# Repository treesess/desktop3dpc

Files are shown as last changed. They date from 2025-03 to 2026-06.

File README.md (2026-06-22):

# desktop3dpc - vcp (vibration cementitious printing)

desktop scale 3d printing of cement-based/non-Newtonian materials (e.g., cement paste, mortar, concrete) using a vibration unit in the toolhead to make the fluid down from the nozzle. 

 **check out the latest version of build:**

- [vcp voron, r11, integrated hopper-nozzle design but no hotend, easy assembly, friendly for starters](https://github.com/treesess/desktop3dpc/tree/main/vCP260622%20vcp%20voron%20r11)
- [vcp voron, r9.3, stable version with hotend, difficult to make and assemble](https://github.com/treesess/desktop3dpc/tree/main/vCP260419%20vcp%20voron%20r9.3)

This page is basically a journal, updating the latest works. 

-------
**260622 update:** 

vcp voron r11 (integrated hopper-nozzle design but no hotend, friendly for starters) has printed 100% size benchy successfully. CAD file has been uploaded. major updates of the design has been documented. 



cosy ship, huh. well, first time for 100% size benchy, so yeah again, room to improve as always. 

i just came to realize that for a print this small, i should turn off the heat bed and pause every single layer and blow it with heated breeze (i.e., hair blower). haha, it worked. 

and keep blowing heated breeze might also work. but it must have programmed pooping and/or wiping to avoid clogging. to be updated later... not likely to add a part fan on the toolhead but more likely to get it a side fan with heat. 

as i said, water control is the center of desktop cementitious print. and heat is one major way to control the water content in the printed part, no matter via hotend, heat bed, or hot side fans. 

the hotend version is not forgotten. since hotend is a better plan than the hot side fans because the side fans cannot blow the heat INTO the printed part but the hotend can extrude uniformly heated slurry and also better for hydration and strength growth. 

-------
**260611 update:** 

vcp voron r10 is on hold while r11 is under heavy tests. 

- r11 is much simpler to make with the hopper, barrel and nozzle printed in one integrated part.
- r11 is easy to assemble with less metal parts but no hotend.
- r11 is very friendly to the starters. that's why i decided to finish up r11 first. 



full video: https://youtu.be/ELNMFBjC2Hw

in the video all was 140% 3dbenchy printing chips. failures were mostly because of mix matter, or feed screw caused pressure builup (so i started to think it's better to switch the feed screw to stirrer only). and simply the difficulties of printing 3dbenchy. 

i have to say benchy is very hard to print. especially when some of the layers have only a few seconds of layer time. 

is this project/toolhead useless since it cannot even print a nice benchy? well, can clay printers do the benchy? lol. thus, i believe the slurry print of this project has achieved much more than expected. you will love vcp voron r11. 

-------------------------------

**260522 update:** spent 4 hr 42 mins printed this giant thin wall vase. not perfect, but learnt sth more and confirmed that the water content in the print body determines it's being "wet print" or "dry print". Also, the chamber humidity greatly influences the water content in the print body (yea you already guessed that). related Reddit post: https://www.reddit.com/r/3Dprinting/comments/1tkmnuv/desktop_cementitious_print_by_vibration_vcp_voron

starting do the enclosure for this printer with a humidity control plan (no way, i do know humidity control isn't easy. hope the accuracy of humidity control for vcp isn't that harsh).



(left: eSUN PLA+ fire engine red; right: cement paste; both: printed by VORON2.4)

Model credit: A *slightly* Overengineered Olpe Vase by Nat on printables: https://www.printables.com/model/290951-a-slightly-overengineered-olpe-vase-print-in-vase

-------

**260517 update:** vcp voron r10.1 is being tested. so far so good. use 20.5 mm barrel and a feed screw having a large gap with the barrel. 

this means:

a) less assembly precision needed 

b) pressure buildup inside the barrel will be mostly turned into backflow, which means better mixed slurry, and

c) the problem of jam due to pressure buildup will not happen again. 



-------

**260513 update:** layer lines. what layer lines?



mortar this is. added 40-70 sand. 

model: Queer_Qube_Box_50mm.stl by DaveMakesStuff on [thingiverse](https://www.thingiverse.com/thing:6321660).

-------

**260508 update:** have been testing 1.5 mm nozzle using my ocd for days. it's bloody hard and i came along with concepts that i didn't know before. some kind of pressure build-up when using feed screw which caused blockage/choke-up. planning to redo the screw barrel to 20 mm diameter and have more tolerance for the backflow. 



Juliavase and 30 mm VORON DESIGN cube have been printing for days. i will get a perfect one.  

and yes, new feature unlocked: pigment efflorescence (in a good looking way)

-------

**260423 update:** finally got the perfect VORON cube (i mean, the mechanism reached the "perfect" level i expected for months). will still keep exploring. 

check out the video clip on [utube](https://youtu.be/D2BQ4VoVuh0)



-------

**260329 update:** after printing ten plus VORON cubes, i tried a benchy. not that the VORON cubes are not good to show, but i want a perfect VORON cube next time i post it. 



-------

**260208 update:** in case you are interested in how it looks after curing, the photos fyi. smooth skin of it, makes us can't stop rubbing it. 





also the non-vase mode (normal slicing, not using spiral/vase mode) print has been tried. several times: 



hey, it's a VORON cube i believe, i know it's not cool enough... could you pls just give me some credits for trying the predicted disaster XD. 

yes, the flowrate wasn't good, due to, umm, some print parts cracked not long after the start of printing. 

also of also, the MCU error (actually tmc2209 drive error) has been fixed by updating the toolhead - sorry that version is not milestone enough so i may upload an even newer version after finishing the design and test. 

i think i also need to explain why there was stepper drive error. it's some kinda "reverse electromotive force", caused by the obvious - we force the stepper to lose steps all the way, so when the rotor kept bouncing backwards again the drive, thus the "reverse electromotive force". sorry that i can only explain this in a level of "making sense" because i m not a specialist on motors... 

-------

**260108 update:** though the MCU (skr pico) reported error from time to time (possibly due to the intentional step loss of motor), a neat enough one has been printed: 



above is the latest print. 

------

**251007 update:** shore 10 solid silicon rubber (SSR) applied as a buffer to isolate the vibration from the toolhead to the printer frame. Metal nozzle adopted. Vibration motors directly hits on metal nozzle. 4 mm nozzle printed cement paste with a stable flowrate. 



(this was printed by a subversion toolhead, which was not uploaded, but don't worry the current version is much better.)

--------

below is my first print:



1) put a vibration device just above the nozzle. not a stirrer but an actual vibrator. 
2) heat bed on, like fdm

in this way, you can easily print cement-based stuff to whatever height you want on a desktop. 

no need of any additions (e.g., PFA, GGBS, silica fume, plasticizer, AC, balabala), just OPC and sand can work this through. 



i used modified CR10s as the motion system, changed the toolhead, and printed about 300 mm wall in vase mode with about 20 mm thick of width. 

you may see the flow rate unstable in the picture, that's because i just came up with the vibrator idea last night and was controlling the flow manually. surely will do a better control of flowrate. 

-----

the advantage is clear: 

1) no need of pump, which is a must in industrial printers.
2) no need of additions, which make it pretty easy for raw material prep.
3) water/cement ratio can be seriously low. 
4) Klipper firmware and fdm slicer can do most of the gcodes, easy for turn a digital obj into print file.
5) simple toolhead, basically every fdm machine can be modified into a cementitious material printer with a slight change of toolhead.

----

note: 

1) for sand, you better sieve it into 0.3 to 0.6 mm size. of course, if you use a larger nozzle, you can even do coarse aggregate (5 mm or above).
2) heatbed greatly reduces the first setting time of the fresh mix. but it might affect the final strength of the print. however, it's desktop, you want the shape but not the strength, don't you?

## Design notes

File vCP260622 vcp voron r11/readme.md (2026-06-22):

r11 is a plastic nozzle version without hotend to heat up the nozzle but very friendly for starter to build. low cost and easy manufacture/assembly.

documentation in coming!

if anything doesn't seem right, my apologies. please let me know. Thanks!

-----------------------------------------

# 1 toolhead, vcp voron, r11

just a second for the naming of vcp voron: vcp is short for vibration cementitious print, vcp voron is like E3D Revo Voron, means vcp *for* VORON since it's based on VORON2.4 motion system. previously there were vcp on a CR10 but that's not reliable since the bed of i3 motion system is not good for the fresh slurry print to keep its shape. so basically vcp is just for VORON (or delta, but still DORON Velta would be nice). 

## 1.1 toolhead intro

i hope this intro shows you how this toolhead works. parts were put into folders.

### 1.1.1 x carriage

based on the x extrusion and MGN12 linear rail of VORON2.4r2.



### 1.1.2 positioner

to make the major functional part in position, as well as connect to PG13.5 umbilical cable mount. 



### 1.1.3 integrated hopper-nozzle

cementitious slurry goes in from the top and comes out from the bottom. 



### 1.1.4 hypocenter

this group generates pulse vibration by forcing step loss of the stepper. no worry about the counter-EMF (counter-electromotive force), the 608 bearing limits it and i tested it.



the hypocenter has been working very stably through many versions in the prototyping. the hitter is an M3x50 screw with many shims to thicken it a bit.

### 1.1.5 (optional) upper drive

actually became optional. the major function of this part is to keep stirring the slurry so that it won't settle in the flow path. you can do the stir-up manually without this part. 



for nozzle diameter smaller than 1.5 mm, it's NOT recommended to install this part (and yes stir up the slurry manually would be an better option, i will explain why later (maybe...)).

### 1.1.6 (optional) LED light bar

have a better view. 



### 1.1.7 (optional) resin coating jig stand

if you want to finish up the surface with epoxy resin, you may use this jig. 



# 2 hopper-nozzle body

slurry feed hopper with integrated nozzle printed in one part, brings you a continuous and seamless flow path with smoothness. 

### 2.1 FDM print of hopper-nozzle body

recommend ASA or at least ABS print of the **hopper-nozzle body** because cementitious material is alkaline (pH 12-13 for fresh slurry) therefore PETG or PLA won't survive too long. 

0.2 mm layer height is good. recommend 0.5 mm line width for both inner and outer walls with 7 walls at least, because it's gonna stand against frequent impact pulse vibration during the print. 

after print out, directly screw in one M3x20 SHCS (socket head cap screw) near the nozzle as a reinforcing bar, like this: 



(do not over-fasten this screw, it's plastic anyway. over-fastening may cause interlayer cracks in the print part)

### 2.2 (IMPORTANT) internal flow path finishing procedure

the flow path needs to be smoothed by drill bits, 60° chamfer drill bit, files. the roughness of the flow path will cause flow rate inconsistency and/or material buildup and/or clog. 

tools need: 



- hand-held electric drill (better have 2 sets)
- 20.5 mm 60° 3-flute chamfer drill bit  (*filleted, extended*) - M3 or M4 tapping tools are needed to extend the length of this bit (see photos below)
- (optional) 20.5 mm drill bit
- hex shank screwdriver bit extension
- hex shank socket wrench 
- round file
- nozzle-diametered drill bit (e.g., 1.0 mm drill bit if you want 1.0 mm nozzle diameter)
- (optional) carbide rotary file (pointer)
- 4-flute taper reamer with hex shank socket (*tip sharpened*)

(optional but highly recommended) you may use an angle grinder and sandpaper to do a fillet on the sharp edge of the 60° chamfer bit. this can give you a smooth transition of flow path. 



a light torch is recommended if you wanna have a look of the flow path:



#### 2.2.1 section one - barrel

you can consider using a 20.5 mm diameter drill bit, but personally i only use the 20.5 mm 60° chamfer drill bit. 

(optional) 20.5 mm drill bit: 



(must) 20.5 mm 60° chamfer drill bit:



i recommend doing this section dry.

if you ever have the other way to drill it down to the throat of the flow path, you don't need to do the extension of the 60° chemfer bit. if not, my plan is tapping the hold of chamfer bit and use an M3 or M4 SHCS and hex shank extension to reach the throat. 

hold the print part and drill in the chamfer **slowly**. 

**PLEASE BE SLOW**. or you may hurt yourself or waste the print part.  



don't do it to the throat in one go. drill in 10 or 20 mm and retreat once. repeat  till you see something like below, you've reached the throat: 



#### 2.2.2 section two - throat

these three are for the throat:

- 4-flute taper reamer
- round file
- (optional) carbide rotary file



if you have the carbide rotary file, you may not need to sharpen the tip of taper reamer like i did. if you don't have the rotary file, you may need to shape the blades on the tip of the reamer. 

let me know if you have better tools for this job! 

for this part, sorry that there is no good photo to take since it's deep inside. 

for me, i use the round file as a probe to grope 



there should be NO STAIR(S) on any transitional part of the flow path. any stairs are meant to make some material buildup during slurry printing. 

#### 2.2.3 section three - nozzle

slowly, drill in your preferred diameter drill bit from the other end like this: 



again, it's better to advance 2 mm and retreat once. repeat till you get it through (to the throat). 

#### 2.2.4 repeat section two and section three multiple times

please repeat section two and section three multiple times and end it up with section two as a finishup. i don't know how to explain this. hope i m scientific enough. 

test it with water. water goes in from the hopper end should be able to come out from the nozzle by gravity:



### 2.3 outer perimeter of nozzle

this is how it looks like when finished with the above steps:



we need to cut it sharper. theoretically, anything sharp enough can do this. you can even use a soldering tip to do this (but i don't recommend that). 

my choice is ultrasonic cutter (e.g., Magicutter): 



the ultrasonic cutter is easy to use and can slightly melt the ASA print making it smoother. 

make the nozzle perimeter as thin as possible (the thinner the better print quality but harder to make): 



(optional) you may file the perimeter a bit if you like: 



then sanding it with at least 2500 grit sandpaper **with water**: 



this would be okay (the perimeter should look polished): 



### 2.4 buffer for positioner

i use PTFE tape as buffer. you can also print a TPU one (like the one in r9.3).



(optional) and wrapped up by some kind of tape that water cannot wash away: 



(optional) better write down the nozzle diameter on the body:



### 2.5 bearing retainer

M3x4x5 VORON standard heat inserts set in the FDM printed bearing retainer part. also here are one 608 bearing and two M3x40 SHCS.



preload the 608 bearing into the retainer: 



screw up the two of M3x40 SHCS: 



### hypocenter

*to be continued*

*to be continued*

*to be continued*

now it's ready to be installed on vcp voron toolhead.

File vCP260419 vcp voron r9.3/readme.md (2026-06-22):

r9.3 is a version you can build and do stable prints. 

documentation for details coming soon. 

if anything doesn't seem right, my apologies. please let me know. Thanks!

# 1 basis of slurry/cementitious printing (IMO)

## 1.1 FDM and slurry printing

hope these texts help you understand the essence of printing. 

with the same kind of motion system, FDM and cementitious printing are quite alike. the differences are:

FDM is centered on **heat**:
- heatsink
- hotend
- heater bed
- melting point (despite plastic types, heat determines the flowability of plastic) 
- chamber temperature
- part cooling (heat dissipation)
- balabala you name it

cementitious printing is centered on **water**:
- water/cement ratio (or water/binder ratio)
- water evaporation
- hydration (chemical reaction between water and cement to get hardened)
- viscosity (despite ingredients, water determines the viscosity of slurry)
- heat (heat accelerates water evaporation)
- breeze (accelerates water evaporation)
- potato flour in breeze (absorb the water on the extruded slurry)

though heat and water are two different things, however, the logic is the same: *we want it to be liquified to extrude, and solidified to fix the shape.* FDM does it via heat, cementitious printing cuts it via water. 

by applying heat to cementitious printing, there might be concerns about strength compromises. yes, if you heat up the slurry too much, bad things happen (cracks, hollow inside with thin crust, lower final strength etc.) imo these can be handled by adding UEA, SF, etc.

surely you don't want to cook the slurry. the strength matters are actually demand matters. what is the print for? answer this then consider heatup or not. heat is to make the print much faster, but not a must (especially when you don't like it (but i do like it xd)).

## 1.2 mix design

mix design refers to the composite of your mix. i will try list the items i know (correct me if wrong, i m just an amateur). 

| item | purpose |
| --- |  --- |
|water| to hold everything together, the pure the better|
|OPC (Ordinary Portland Cement) 52.5 N  |major binder, react with water to build up strength (hydration reaction) |
|PFA (fly ash) |  secondary binder, helps with crack, makes the slurry less bleeding etc. |
|GGBS |  secondary binder, get strength somehow faster comparing to adding PFA |
|sand |fine aggregate, imo make it easier to print|
|stone |coarse aggregate, often larger than 5 mm diameter， thus not likely to use on desktop level, unless you are printing something rough with nozzle diameter larger than 10 mm |
|SP (superplastisizer) or plastisizer (liquid) | make the slurry better flow with less water |
|retarder | similar to SP, but slows down the chemical reaction to buy your longer printing time|
|SF (silica fume) | fine particles help to get compact print|
|quartz power 325/600 mesh | filler, makes the print compact|
|UEA U-type expansive agent | avoiding crack, very useful|
|iron black, iron red, iron something |pigment. may need more water if you add pigment |
|...|...|

## 1.3 how to start first mix desgin

if you are not familiar with cementitious, start with an easy one using only OPC, water, and fine sand (40-70) is totally okay even for 1.5 mm diameter nozzle. recommend w/c = 0.4~0.5, cement to sand 1:0.5 for starter. if you find it hard to mix up (too viscose), try adding a bit more water is fine. weight up mass but not volume. 

if no retarder or PFA added, you have about 1 hour to print. the longer you wait, the harder the mixture is. if you try to add more water after 1 hour to make it printable, the final strength is likely to be compromised somehow, but you can do this for the first several prints since you will need some time to feel and understand it. try and error with more or less water is a good exercise to grasp it. 

if you can handle printing the simple formula, then go considering adding UEA, SF, and retarder to get better/consistent print quality. 

if you are an expert, don't take anything i say seriously and correct me if anything is wrong. Appreciate it. 

## 1.4 how to mix

**safety/health first, get N95 dust mask to protect your lungs.** protective glasses, nitrile gloves (cement-based materials are alkaline (pH value can get to 13)). well, this is the highest standard of protection maybe. personally, i would also recommend gentle, gentle, gentle handling of all the powders to avoid dust flying up. 

dry mix first, wet mix next. 

- dry mix means get all the solid particles measured by mass correctly in a container, then gently, gently, gently mix them up. the colors of different ingredients are likely to be different, so if the final color is uniform, your mix should be fine. do more mixing if unsure. take your time.
- wet mix means adding water to the well-mixed dry mixture from the previous step. prepare your clean/pure water with SP or retarder before adding to the mixture. you may use a syringe/pipet to add the exact mass of water (and other liquid additives) as designed. still, gently, gently, gently add water into the mixture. take your time. start the wet mix slowly. after you see no dry particles, you may mix it faster.

if you add SP or retarder, you may also need to mix for a longer time. by adding retarder, you may use less water and have very long printable window (like 2~3 hours, i tried 5 hours tops, but that was bad). for large prints, i would prepare the dry mix in separate covered containers in the first place, then only add water for wet mix when needed during printing. try not to wet mix over 400 grams anytime. for me i wet mix 100 to 200 grams per batch. 

these are the basics to start with. i think you can start your first mix safely with these recommendations.

for more details, please find tutorials or your expert friends. welcome to email me any questions. 

one further tip here: if you use sand, note that sand absorbs water and releases the air inside it. therefore, you need to vibrate it before your actual printing. i just put the mixture into the toolhead hopper and start extruding/vibrating, then catch the slurry from the nozzle back to get rid of the air bubbles. so is the coarse aggregate. 

---------------------

# 2 vcp toolhead

## 2.1 toolhead intro

i hope this intro can show you how this toolhead works clearly. parts were put into folders. 

### 2.1.1 x carriage



based on the x extrusion of VORON2.4r2. 

### 2.1.2 positioner



to make the major functional part in position, as well as connect to PG13.5 umbilical cable mount. a thick TPU ring is between the major part and the positioner as a buffer. 

### 2.1.3 feed screw and barrel



paste put in here. this group includes the feed screw, screw barrel, stepper, Orbiter planetary gearbox, stirrer, etc. the feed screw provides better extrusion accuracy. the stirrer avoids material buildup inside the hopper. the stepper and the gearbox drive them. 

### 2.1.4 hypocenter



this group generates pulse vibration by forcing step loss of the stepper. no worry about the counter-EMF (counter-electromotive force), the 608 bearing limits it and i tested it. 

### 2.1.4.1 stepper with hitter 



sorry i don't know how to name it. this group inside the hypocenter has been working very stably through many versions in the prototyping. the hitter is a M3 screw with many shims to thicken it (try any other metal way to make it as you want). 

### 2.1.4.2 608 clamp and hotend



the hitter driven by the stepper hits the 608 bearing, where the heat block is locked tightly by 3x M3 screws so that the vibration can be passed to the nozzle in a rigid structure. the heat block is the CR10 one. the nozzle is SUS304 tube been cut and tapped with M6 threads. 

-------

## 2.2 make of toolhead parts

### 2.2.1 FDM printed parts

- since almost all parts are under cyclic load, ASA is recommended for the printing of vcp voron toolhead with 0.3 mm layer height. 
- for the barrel/hopper one, 0.1 mm layer height is recommended to make a smooth inner surface of the barrel as possible.
- for the feed screw, 0.1 mm layer height is recommended. better sand it smoother. 
- get some more perimeters and higher infill percentage as possible. sorry i don't have tests to tell how strong they need to be. 
- there is only one TPU part. you need to cut it vertically after print. if you don't want TPU, you can just use some tapes (PTFE Tape i recommend).

### 2.2.2 metal parts

- the M3x100 SHCS needs to be straight.
- the M3x100 SHCS needs to be straight. 
- the M3x100 SHCS needs to be straight. 

this M3x100 is to strengthen the feed screw. i may try metal print of the feed screw later. 

### 2.2.3 heat set inserts

only the "standard VORON heat set inserts" M3x5x4 mm is used. 

- 4.6 mm holes are for heat inserts
- 5.7 mm holes are for SHCS caps

*to be con't*

-------

## 2.3 toolhead assembly

there is no screw must be fastened very tight to make it work. overtighten might cause plastic failure or fail of assembly (i've been there). 

### 2.3.1 x carr 



- 2x M3x40 SHCS to assemble the left and right parts.
- 4x M3x8 SHCS to fix the x carr parts to MGN12H slide block with belts through. similar to the original x carr. 

btw i kept the 32.5 mm horizontal distance of screw distance for the x carr but the failed to follow the vertical distances. 

if you need to change the x carr frequently, i would recommend marking the belt as in the photo. 

### 2.3.2 hypocenter stepper w hitter



### 2.3.3 pancake NEMA 17 w Orbiter planetary gearbox (8 mm shaft)



### 2.3.4 hotend (2x CR10 heat blocks)



drill out the M6 threads of the upper one or not seems does not matter. 

### 2.3.5 feed screw w stirrer



get a 0.5 mm M3 shim in between the feed screw and stirrer is recommended. 

### 2.3.6 coupler



screw the M3x100 tight now. but not too tight to break the plastic...

### 2.3.7 to the pancake



### 2.3.8 into the screw barrel



### 2.3.9 tight up pancake mount



check if you can rotate the feed screw and stirrer manually. if you can't, try loose the four mount screws a bit. 

the feed screw should not have relative rotation to the stirrer. or you need to check step 7. 

### 2.3.10 hypocenter motor



watch out the cable exit and hitter direction. 

if you feel it time consuming to screw in these two M3, just drill the motor mount with a 3 mm drill bit. 

don't overtighten these two M3. 

### 2.3.11 checkpoint



### 2.3.12 nozzle



it is SUS304 tube, OD 6 mm ID 3 mm. thread the tube with M6 so that you can get it into the CR10 heat blocks. the total length doesn't have to be accurate. not even the length of threads. just about 40 mm long is fine. you will find out why when you finish the assembly and G28 z. 

### 2.3.13 nozzle assembly



screw the nozzle into the CR10 heat blocks and push it into the lower end of barrel. there should be a small gap as shown in the photo. don't really matter how large the gap is. or you can use a feeler gauge to be certain. just define the gap by yourself. sorry i m lazy to do that. 

### 2.3.14 secure the nozzle



- two M3 screws first
- M6 nut later

### 2.3.15 608 clamp







set steppers off, and move the hitter manually. it should be free to move several millimeters with the limit of 608 bearing. if it's too tight to move it. try loose the two motor screws a bit or the clamps and twist it a little. 

### 2.3.16 TPU buffer



### 2.3.17 fake position



since i don't have xyz endstops for now. i fake the position at 150 0 0 and manually set z offset. there is no QGL so far. sorry. 

### 2.3.18 tighten up the positioner parts



and the PG13.5 umbilical cable mount. 

the optional COB LED light bar is also included in the cad file .f3d. just hook it up if you make it too.

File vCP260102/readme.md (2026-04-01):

this is a vCP-e version where e for extruder axis in use. That is, FDM CAM slicers (e.g., OrcaSlicer) with default E gcode generation can be directly used for this toolhead in a print. 



yes it's already this good without detailed tuning. check out how it moves: https://youtu.be/I5zWxPGP2qw 

the greatest benefit of using E axis in FDM slicer is that, you can do perfect *TRAVEL*, i.e., you can move your toolhead without leaking a single bit of cementitious mixture! 

recommended Klipper configuration for extruder:

```
rotation_distance: 5  ; this affects the pulse your drive sends to the motor if i m not wrong. to be simple, the smaller this is, the higher frequency the stepper does. 
microsteps: 8   ; or 16 is fine if your MCU doesn't report errors. 
full_steps_per_rotation: 200    ; for 4240 1.8 degree stepper motor
; gear_ratio is not needed

```

and its drive: 

```
interpolate: False  ; i don't know, LLM told me so
run_current: 0.5   ; worked longest for me. smaller run current can make your stepper not that easy to fail under fatigue caused by cyclic impact loading. 
hold_current: 0.5  ; better keep it same as the run_current

```

All CAD and 3MF uploaded for your reference. this version is much stabler than any of the previous versions (including many versions never uploaded...)

BOM of this toolhead: 

| name | qty. | descriptions  |
| --- | --- | --- |
| stainless nozzle |1 piece |dimensions pls see the f3d CAD file thx|
| steel rod | 1 piece |diameter of 6 mm, length of at least 40 mm (hold it, you may need longer for the next version...) |
| M3x80 SHCS | 2 pcs  | for the upper part of mounting|
| M3x50 SHCS | 2 pcs  | for the lower part of mounting |
| M3x8 SHCS | 7 pcs | |
| Heat set inserts (M3 Threaded Insert ) | 3 pcs | The VORON "standard" ones (M3x5mmx4mm)|
| LSR (liquid silicone rubber) | 7 pcs |  20  degree or lower. 50 grams (A+B) is enough for one cast of the rubber buffer parts|
| stepper motor |1 piece |  4240 or longer | 



printing recommendations:

- PETG is recommended for all the parts. 

- Only the bowl part needs a bit support (sorry for that, i don't want to but that's quicker. and i m not sure if the ears of the bowl can be cut off. better have them to simplify the installation). All other parts can be printed without support. You can use PLA to print the molds for LSR if stringing is a big issue for you. 

- maximize the wall/perimeter counts for all parts (except the "front" part) since they are going to suffer from heavy fatigue loading. i ve made them skinny as i think good enough so even if you print all parts in 100% plastic inside, it's not much heavy.



for the "bowl" part, only a bit of support have been painted in the .3mf fyr. 

for casting LSR, please screw your long M3 SHCS into the molds first, similar to the below photo (sorry that the below photo is showing a previous version but i m sure you can get what i mean): 



more info about using SSR for vibration buffer can be found [here](https://github.com/treesess/STEAMRELAY/tree/main/showcase/251003%20vibration%20absorbing%20design%20using%20SSR)

------------

still testing stuff. but the news is, this version of toolhead is still not my ideal plan. new toolhead is on the way.

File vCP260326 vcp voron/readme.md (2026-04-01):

finally i've got a stable version of toolhead. still, too many to improve, trying very hard every day. 

pls see the f3d CAD file for details. 

if you wanna build one, please let me know and i will sort things up and upload them for you. 



The motion system is VORON2.4. X carriage is in the f3d as well. For the modification of bed into a seperate/independent one (to isolate vibration from the frame to the bed), i used a piece of concrete and 4 rubber footpads, not a neat design, may upload later. 

## 1 Explanation of how this toolhead works

1) generation of pulse vibration

Using an M3 bolt as the oscillating impactor, repeatedly tapping the inner race of a 608ZZ bearing to induce periodic (pulsed) vibrations. This M3 impactor was driven by the 42 stepper. The 42 stepper simply executed the gcode of normal E instructions but lost most of the steps due to the constraint of 608 bearing. 

the 608 bearing was tightly constrained with the heat block. the SUS304 tube was tapped and screwed through the heat block. in this way the pulse vibration was passed to the tube. 

2) flow path

the mixture was added into the hopper. since the vibration of the toolhead, the mixture went down by gravity then entered the SUS304 tube. the lower end the the tube was the actual nozzle as the exit of mixture flowing on to the print layer. 

3) why vibration works

cementitious materials are thixotropic, simply speaking they stay sold when static, but become fluid under vibration. we control the vibration of this toolhead, when the toolhead moves to the position to extrude, vibration starts so the mixture become fluid therefore goes down under the gravity. after the extrusion, the mixture stays on a static bed, therefore becomes quite solidified to support other layers. we can do travel without extrusion with the same logic. as long as we don't vibrate, there is no extrusion. 

4) heatbed and hotend

heatbed with 50 to 70 ℃ can accelerate the hydration of cementitious materials. hydration is the chemical reaction that makes the cement-based mix sold permenantly. but temperature too high may cause shrinkage of the print. in real case this doesn't hurt too much because the new layers bring water to the previous layer, to keep it wet. however, overall speaking the chemical reaction needs water to go on, therefore at some point we add water to the print to keep it wet. this is subtle, can only spray a bit because too much water will destroy the print since it needs hours to complete initial setting. the print is vulnerable before that. that's why we need a separate/independent bed for it. 

hotend is experimental. as we heat up the mixture in the toolhead, it increases the workability of mixture and makes it easier to extrude. higher temperature also makes the extruded part cure faster. but there are problems with this doing. if the mixture has been staying in your hopper for too long (1 or 2 hours), it's partially cured, higher temperature make this quicker. the worst case is, when you pause the print, the mixture near the nozzle may complete the initial setting and block your nozzle. 

both heatbed and hotend have another problem, that, higher temperature dry up the mixture and print fast. we really want to keep the water in our mixture because that makes the viscosity stable thus stable flowrate. but heat evaporates the water so this is a subtle balance game. 

5) printing

it is very similar to FDM printing. but much slower. 10 mm/s speed is considered high to me. if one layer has its layer time under 1 minute, it's very likely the next layer will drag it forth and back. so i recommend making a PAUSE to these fast layers. i don't recommend you to slow down these layers since you will need to tune the flowrate for different speed. 

large overhang and medium bridge are all possible. because the mixture is sticky. you may easily print a large overhang successfully, but please wait some time before printing the next layer because it needs more time to set. if you don't wait, the next layer might crush your beautiful overhang. same thing to bridging. 

for large area of bridging (such as the ceiling of 3dbenchy, 250% size), it's totally possible, but, you need to PAUSE every 2 to 3 lines. or the next line may drag the previous line down. 

(to be continued)

## 2 cement paste mix design

i used a simple mix for multiple print tests so far. 

| item | gram | descriptions |
| --- | --- |  --- |
|OPC (Ordinary Portland Cement)|100|major blinder|
|PFA (fly ash)|40|secondary blinder|
|water|50| may add more if your mix is too viscous|

adding river sand (fine aggregate) can improve print quality greatly sometimes, but make sure your sand particles are much smaller than your nozzle diameter (at least 1/2 or 1/3). reduce your water/cement ratio to avoid bleeding and segregation. 

(bleeding means water comes up when vibrating, segregation means aggregates sink down when vibrating.)

(to be continued)

------------------

**important note: everything is still experimental, though this version is basically stable but still need long term tests to prove the robustness which in still ongoing**

## 3 BOM

| item | qty. | descriptions |
| --- | --- |  --- |
| 608zz bearing  | 1 |as the constraint of M3 impactor |
| SHCS M3x100 | 2 | fastening the heat block to the hopper |
| SHCS M3x70 | 1  | ditto |
|SHCS M3x35 |4 |fastening the front and the toolhead to x carriage |
|ASA or ABS filament | - | for printing toolhead components, PETG is not okay with highly alkaline cementitious mixture|
|TPU filament |-| for printing the buffer cylinder which holds the major part|
|SUS304 tube od6 in3, 112 mm long|1| lower end as the nozzle, upper end connects to hopper, you may need longer or shorter depending on bed setting|
|42 stepper |1 | to drive the impactor (hitter in CAD) |
|...|...|...|

(to be continued)

## 4 tools
| item | qty. | descriptions |
| --- | --- |  --- |
|angle grinder|1|you may need to cut or grind the hardware|
|taper reamer bit|1|for chamfering the hopper to make it smooth|
|chamfering bit 60 degree |1| for chamfering the SUS304 tube |
|round file 600 grit|1| to make the tube smoother even|
|1000 to 5000 grit sand paper|1|to make the tube extra smooth|
|angle grinder|1|you may need to cut or grind the hardware|
|allen key|1 set| for the M3 bolts|
|hex bit and screw driver|1| some M3 bolts are too long to be driven by hand|
|containers and mixing knife|3|for mixing cementitious materials, get some spares|
|digital balance, 0.1 g resolution|1-2|for weighing up raw materials for mixture|
|bucket with water|1|for cleaning. when a container or tool with mixture is done, put it in water, this makes it easy to clean later|
|tapping tool M6|1|to tap the SUS304 tube|
|drill bits 6 mm|1 set|make the holes on heat block a bit larger|
|...|...|...|

(to be continued)

## 5 assembly

this toolhead needs certain sequence to assemble. 

1) the "compressir" part to hopper with M3x70 bolt. use both M3x100 bolts for alignment. after aligned, tighten the M3x70 then take out M3x100.

2) screw the tube to the heat block. then get the tube through "compressir 2" and the "compressir" and reach the end of hopper.

3) adjust the screw of tube to make it look fit (um... i don't know how to describe here). the tube is expected to be limited by the hopper and there should be no gap between all these parts.

4) two of M3x100 go through both heat blocks and compressirs to the hopper and screw in the heat set inserts.

5) get the TPU cylinder, knife it so that you can wrap it around the "compressir"

6) get the "front" and its retainer (is it right to call this thing retainer?), wrap the assembled part and use 4 of M3x35 screws to position it to the x carriage. don't tighten, we will need to rotate it and making some adjustment later.

7) assuming you have install the impactor on the motor shaft **(more details need to be explained here)**, install the motor mount to the motor. then use two of M3x?? to fix the motor on the "compressir".

8) put 608 bearing to it's clamp and install the clamp to the lower heat block. make sure the impactor go through the 608 bearing. **(more details need to be explained here)**

9) make adjustment to make sure:

   a) the motor body doesn't touch anything;
   b) the impactor can click the 608 bearing manually **(more details need to be explained here)**;
   c) the installation height is good and the nozzle isn't hitting the bed.

11) fasten the front M3 to finish. these M3 can be used to adjust the nozzle to be parallel to the bed. 

(to be continued)

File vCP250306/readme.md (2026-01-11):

this is an OLD VERSION of toolhead, please go to https://github.com/treesess/desktop3dpc/tree/main/vCP260102 to see the current version. 

-------------------

this is the first design of vCP. based on the motion system of CR10s, changed the x carriage and toolhead and succeeded in stable flow rate mortar printing. 

**all CAD STL are open-sourced (GPL-3.0 license) for download. Welcome to build yours and let me know!**

All plastic parts were designed for easy and strong FDM printing without adding additional support. Let me know if you have doubts about which direction to put on heatbed. 





on its second print, using already hardened mixture after 2 hours of mixing, it still printed rather consistent lines nicely. 



note that this was 10 mm nozzle printing 7 mm layer height, which isn't recommended since layer height too large makes very weak interlayer cohersions. 

-----------

here goes a brief intro of how this toolhead works: 



inserted into the bowl is this torsional shaking bit along main shaft. it has some blades, and keep around 5 mm distance to the bowl wall so that the vibrated concrete could be pushed into the "tunnels" to have a more consistent flow rate (at least this is how i think it works, tbh i m not 100% sure if the explanation is correct, but the printing results were seriously good)



The main shaft is a 8 mm diameter rod with M5 nut grooves on both ends. it is constrained by two 608zz bearings from horizontal movement, but free to have torsional movement and vertical movement. 

Then the upper is the vibration motor unit clampe to the main shaft by two M3 SHCS. 

At last the top, there is an F625z bearing and M5 nut holding the main shaft which serves as the "hanger" and adjustment of the vertical positioning of main shaft so as the vibration unit inserted into the concrete bowl. 

The vibration motor is driven by DC power and the voltage can be adjusted by a DCDC module. The voltage controls the rpm/frequency of the vibration unit. 

so far these are my thoughts and put into practice. i m sure there are many to be optimized. and i actually don't know exactly how it works. i can't explain to you why the horizontal vibration of motor can be turned into the torsional one in the vibration unit but this is what happened when i observed in [here](https://github.com/treesess/STEAMRELAY/tree/main/showcase/250119%20mod%20of%20drill%20for%20concrete%20vibration%20in%20plastic%20mold). Maybe it's some kind of crank. idk. please teach me if you have a clue, big thanks!

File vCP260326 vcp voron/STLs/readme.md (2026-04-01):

**These are STLs as the mod of VORON2.4 for cementitious printing. For the STLs of the vcp toolhead, you may export from the .f3d CAD file directly.**

some of the mods are ugly or too simple... just use the ones you feel okay with. 

for the bed, you may simply find some large rubber or wood and place the 8 mm alumium plate on it, my current concrete cast version with rubber footpads is in use only because i found four footpads from storage...

---------

due to my messy management of CAD file and slow computer, there is no single CAD file with all parts. so i'd upload the STLs first. 

allow me to spend time sorting out the CAD...

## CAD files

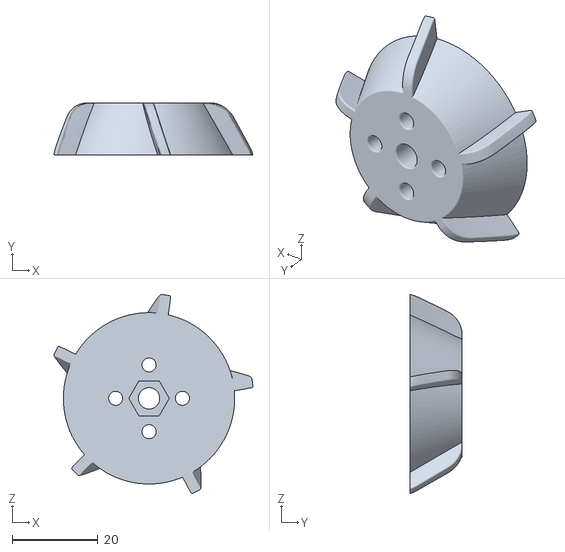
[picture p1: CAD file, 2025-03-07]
vCP250306/vibrator cone upper.stl
46.5 x 12.2 x 46.5

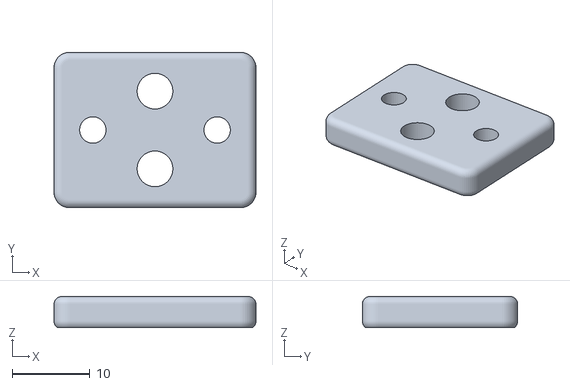
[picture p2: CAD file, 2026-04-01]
vCP260326 vcp voron/STLs/z cable chain end mount x2 (same for both).stl
26.0 x 20.0 x 4.00

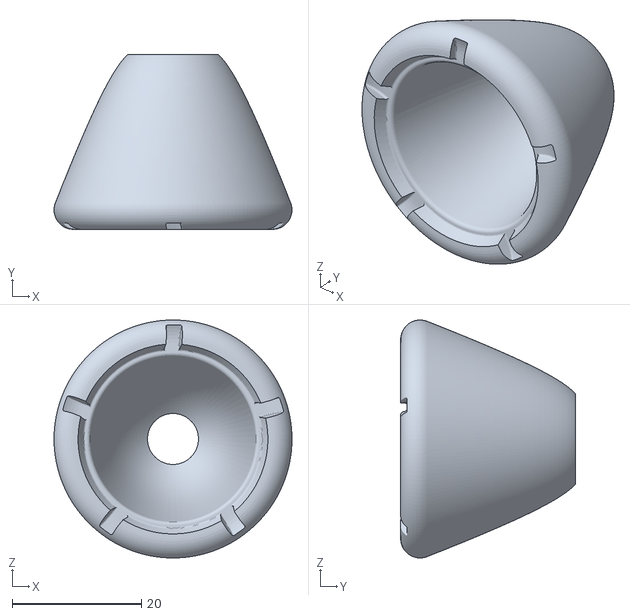
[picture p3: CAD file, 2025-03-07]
vCP250306/TPU cover for vib.stl
36.8 x 27.0 x 36.8

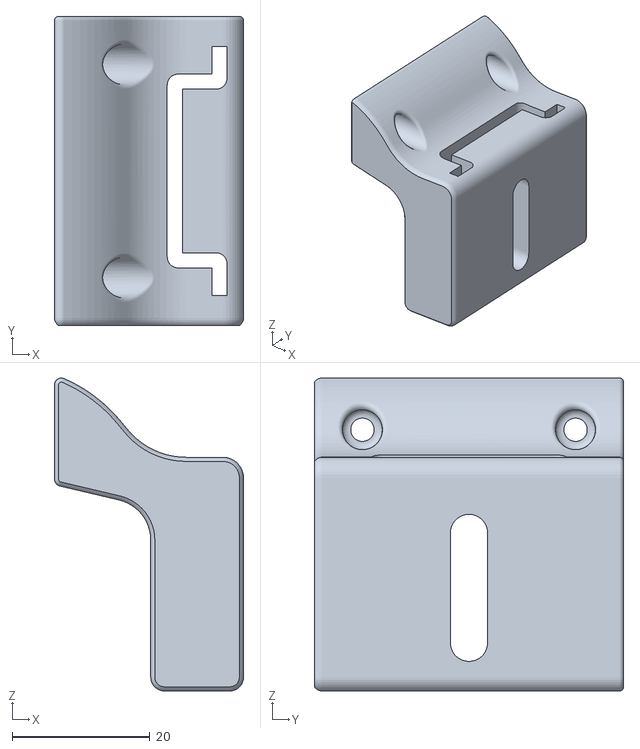
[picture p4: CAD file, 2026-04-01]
vCP260326 vcp voron/STLs/din rail mount to 2020 extrusions at rear.stl
27.5 x 45.0 x 45.5

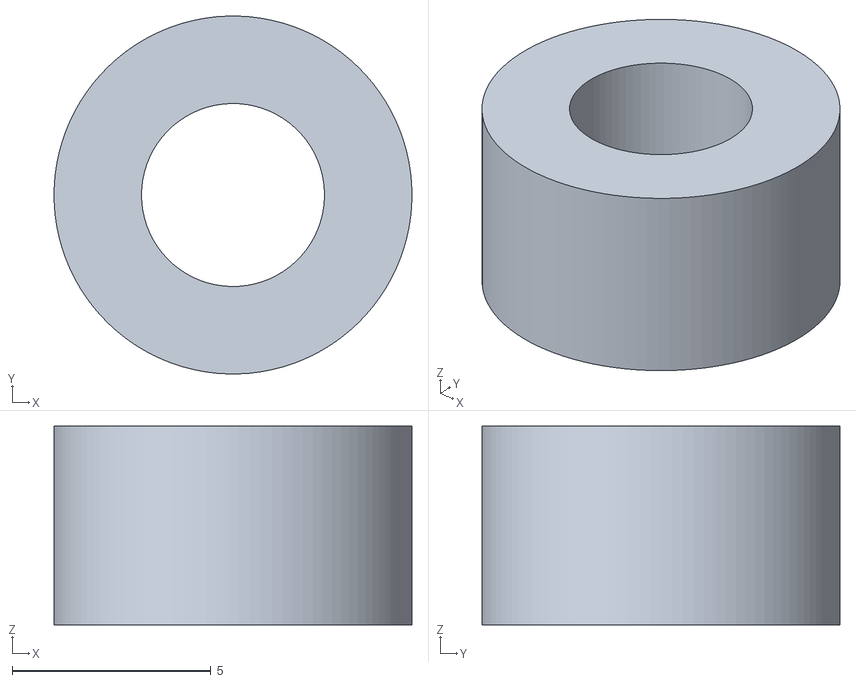
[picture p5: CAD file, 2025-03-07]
vCP250306/spacer 2.stl
9.00 x 9.00 x 5.00

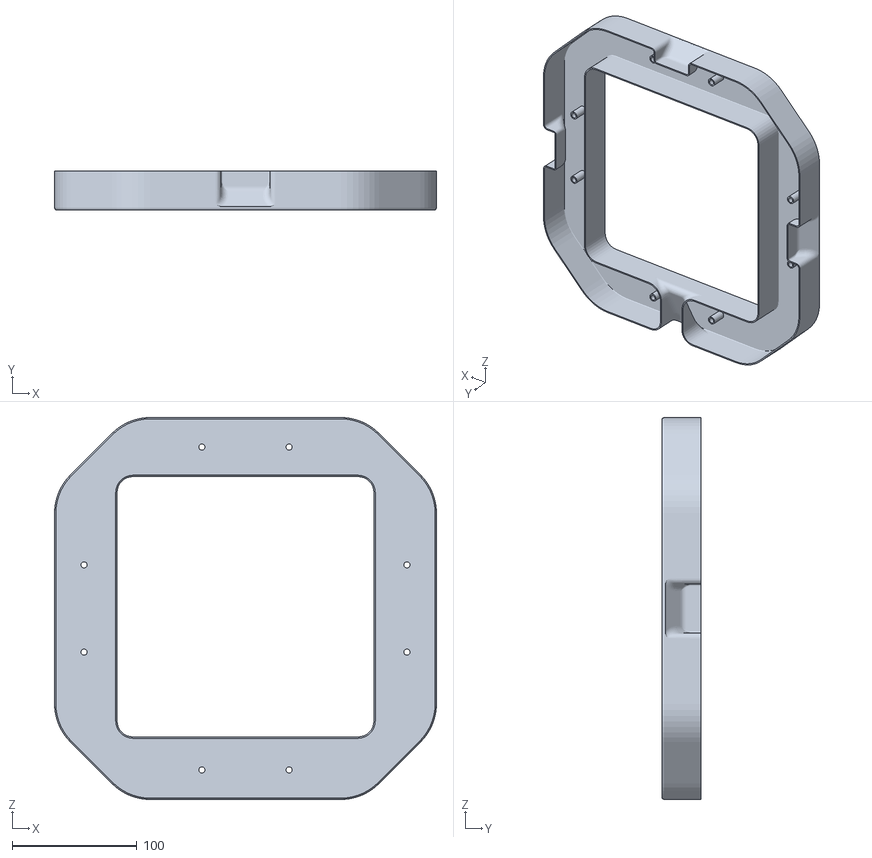
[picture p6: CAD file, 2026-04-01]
vCP260326 vcp voron/STLs/mold for concrete support for bed.stl
306.4 x 31.2 x 306.4

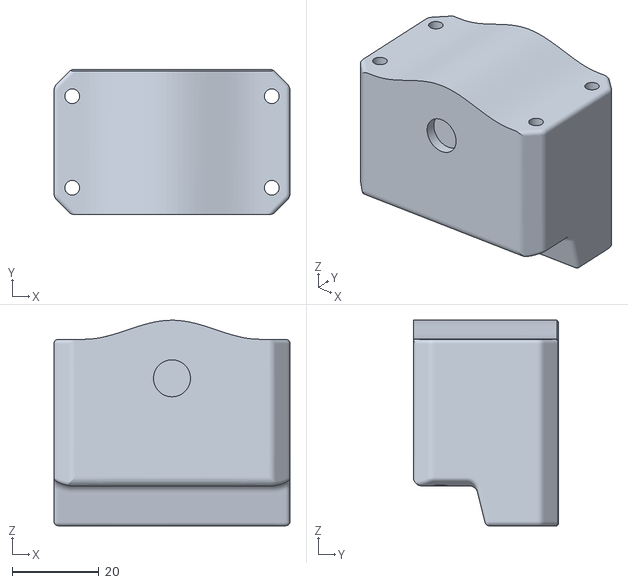
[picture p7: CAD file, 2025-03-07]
vCP250306/608zz fixer.stl
54.4 x 33.5 x 47.4

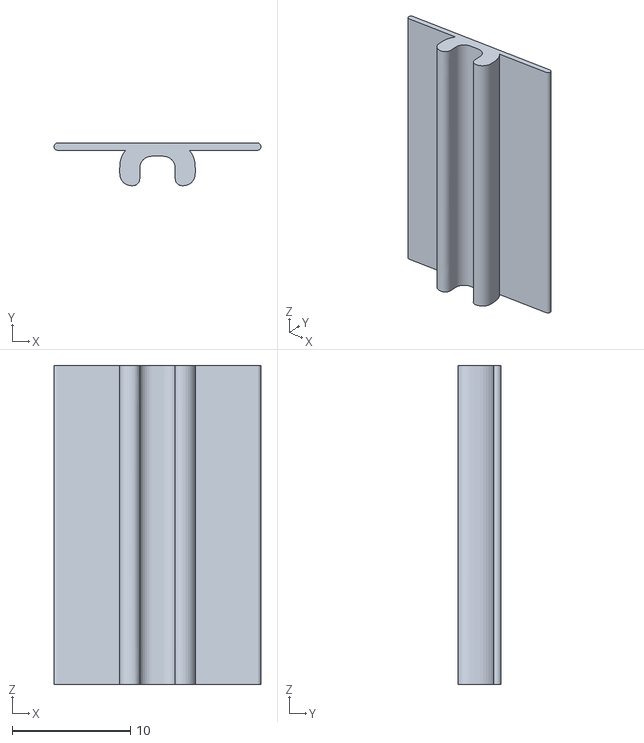
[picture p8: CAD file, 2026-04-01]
vCP260326 vcp voron/STLs/2020 extrusion lower side cable holder (for motor cable, may use TPU to print).stl
17.5 x 3.60 x 27.0

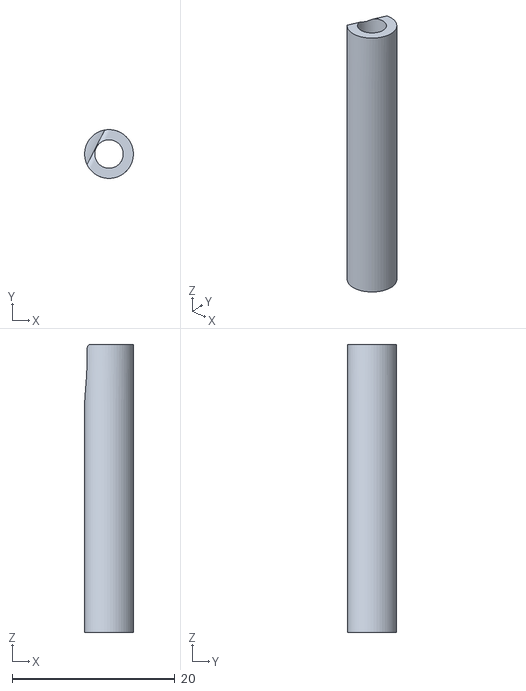
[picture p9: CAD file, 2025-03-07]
vCP250306/spacer 3.stl
6.00 x 6.00 x 35.4

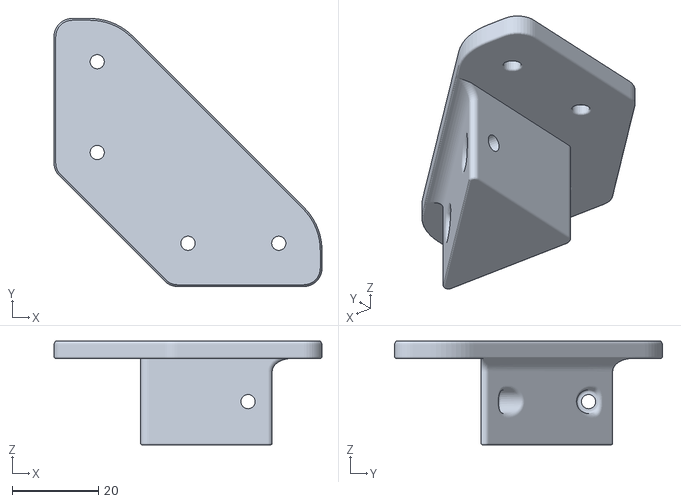
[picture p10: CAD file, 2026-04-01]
vCP260326 vcp voron/STLs/2020 corner brace.stl
62.0 x 62.0 x 24.0

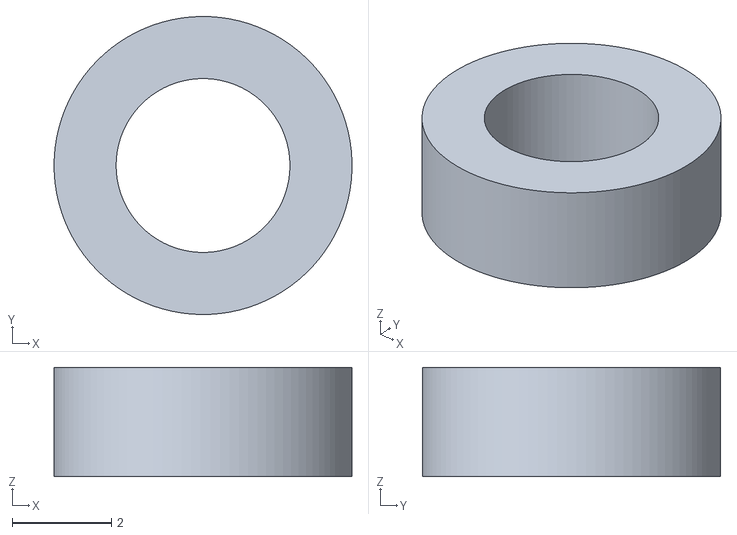
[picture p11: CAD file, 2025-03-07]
vCP250306/spacer 4.stl
6.00 x 6.00 x 2.20

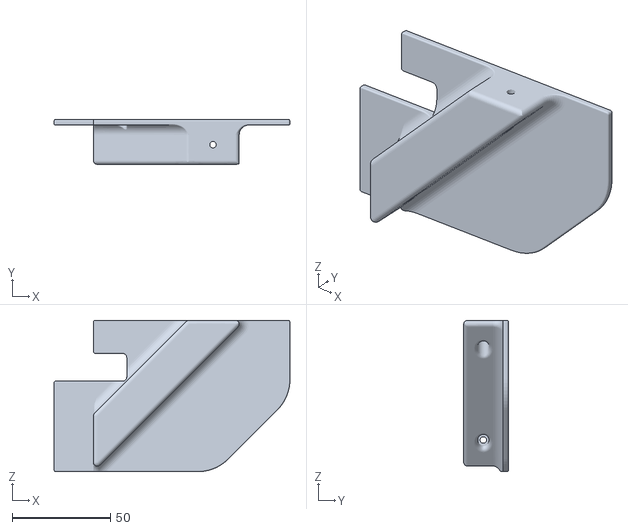
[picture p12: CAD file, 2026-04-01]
vCP260326 vcp voron/STLs/z drive cover rear mirror.stl
120.0 x 22.7 x 77.0

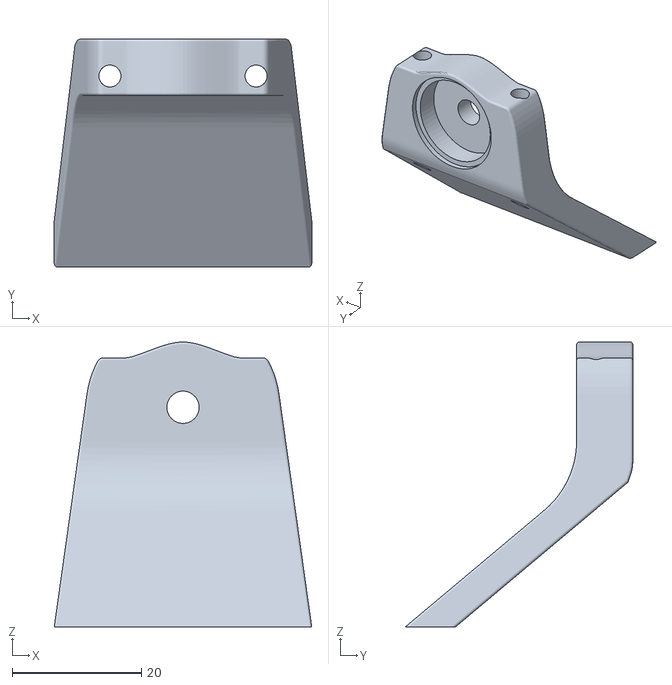
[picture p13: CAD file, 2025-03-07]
vCP250306/vib hanger.stl
39.9 x 35.2 x 44.1

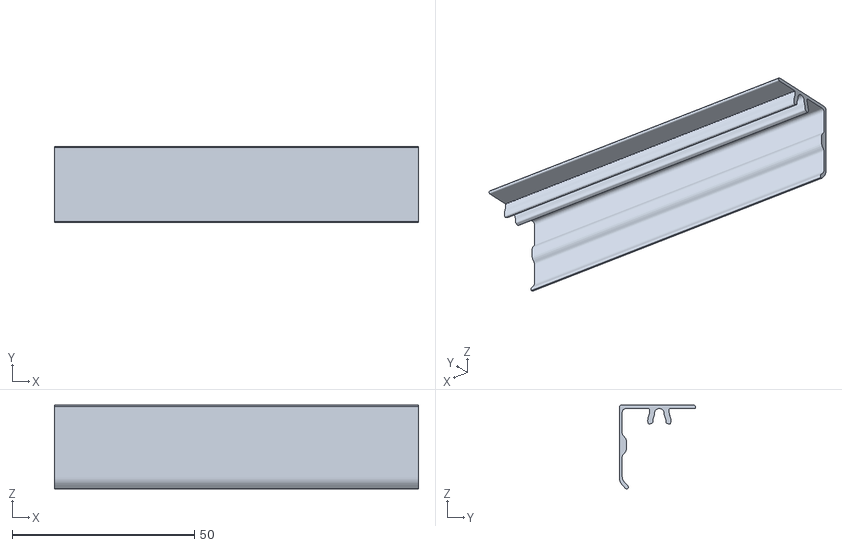
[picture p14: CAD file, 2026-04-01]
vCP260326 vcp voron/STLs/L cover for 2020.stl
100.0 x 21.0 x 23.1

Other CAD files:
vCP250306/x carriage reinforcement.stl
vCP260326 vcp voron/STLs/TPU footpad.stl
vCP250306/vib motor fixer.stl
vCP260326 vcp voron/STLs/flat cover for 2020.stl
vCP250306/barrel.stl
vCP250306/spacer 1.stl
vCP250306/vibrator cone lower.stl
vCP260102/260102 vcp 003-Pen+Holder-Three+Petals+Twist.3mf
vCP260102/260103 fdm4 vcpe by fdm6.3mf
vCP260102/260103 fdm4 vcpe by fdm7.3mf
vCP260326 vcp voron/260326 vcp voron r8.1, nz3.f3d
vCP260326 vcp voron/260328 vcp voron nz3, voron cube n benchy.3mf
vCP260326 vcp voron/STLs/2020 corner brace - plate.stl
vCP260326 vcp voron/STLs/C cover for 2020 for x.stl
vCP260326 vcp voron/STLs/C cover for 2020.stl
vCP260326 vcp voron/STLs/bed concrete support.stl
vCP260326 vcp voron/STLs/bed height adjustment thumb nut.stl
vCP260326 vcp voron/STLs/fly pi lite v2 mount.stl
vCP260326 vcp voron/STLs/z drive cover rear.stl
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

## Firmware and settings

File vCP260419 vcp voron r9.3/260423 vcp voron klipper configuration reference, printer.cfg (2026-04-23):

[include fluidd.cfg]



# [temperature_sensor FLY-Pi]
# sensor_type: temperature_host

# ========================================================
[mcu]
serial: /dev/serial/by-id/usb-Klipper_stm32f446xx_200033001750344D30353320-if00
# CAN bus is also available on this board

[printer]
kinematics: corexy
max_velocity: 300               # 打印机最大速度   
max_accel: 3000                 # 最大加速度 最大3000
max_z_velocity: 40              # z轴最大速度
max_z_accel: 100                # z轴最大加速度
square_corner_velocity: 3.0     # 方形拐角速度，小一点可以有效避免平台重带来的惯性






[idle_timeout]
timeout: 72000    # 3600 = 1 hour 


[force_move]
enable_force_move: True


[gcode_macro FAKE_POSITION]
gcode:
        SET_KINEMATIC_POSITION X=150 Y=0 Z=0
        SET_GCODE_OFFSET Z_ADJUST=10 MOVE=1
        G0 Z10
        G0 Z0
        
[gcode_macro Z_up]
gcode:
        G0 Z10



#--------------------------------------------------------------------
[gcode_macro PRINT_START]          # 将 PRINT_START 设置为开始打印时的宏，自定义打印前的动作


gcode:
    G92 E0                         # 重置挤出
    BED_MESH_CLEAR                 # 卸载网床
    SET_FAN_SPEED FAN=fan1 SPEED=1
    SET_FAN_SPEED FAN=fan2 SPEED=1
    SET_FAN_SPEED FAN=fan3 SPEED=1
    SET_FAN_SPEED FAN=fan5 SPEED=1
    SET_FAN_SPEED FAN=fan4 SPEED=0.12 ; toolhead LED
   ; G28                             # 归位所有轴
  ;  quad_gantry_level              # 龙门架调平
   ; G28                            # 归位所有轴
  ;  G1 Z20 F3000                   # 将喷嘴移离热床
  ;  BED_MESH_PROFILE LOAD=default  # 加载网床
#--------------------------------------------------------------------


#--------------------------------------------------------------------
[gcode_macro PRINT_END]            # 将 PRINT_END 设置为打印结束时的宏，自定义打印完成之后动作


gcode:
    M400                             # 等待缓冲区清除
    G92 E0                           # 将挤出机归零
 ;   G1 E-1.0 F3600                   # 缩回耗材丝
    G91                              # 相对定位
  ;  G0 Z1.00 X20.0 Y20.0 F20000      # 移动喷嘴以移除架线
   ; TURN_OFF_HEATERS                 # 关闭热端
    ; M107                             # 关闭风扇
    G1 Z2 F6000                      # 将喷嘴向上移动2毫米
    G1 Z10 F3000                      # 
   ; G1 Z50 F3000                      # 
    
    G90                              # 绝对定位
    G0  X150 Y20 F3600              # 
    BED_MESH_CLEAR                   # 卸载网床




[gcode_macro PAUSE]
rename_existing: BASE_PAUSE
gcode:
    ##### set defaults #####
    {% set x = params.X|default(5) %}      #edit to your park position
    {% set y = params.Y|default(5) %}      #edit to your park position
    {% set z = params.Z|default(10)|float %} #edit to your park position
    {% set e = params.E|default(1) %}        #edit to your retract length
    ##### calculate save lift position #####
    {% set max_z = printer.toolhead.axis_maximum.z|float %}
    {% set act_z = printer.toolhead.position.z|float %}
    {% set lift_z = z|abs %}
    {% if act_z < (max_z - lift_z) %}
        {% set z_safe = lift_z %}
    {% else %}
        {% set z_safe = max_z - act_z %}
    {% endif %}
    ##### end of definitions #####
    SAVE_GCODE_STATE NAME=PAUSE_state
    BASE_PAUSE
    G91
    ; G1 E-{e} F2100
    G1 Z{z_safe}
    G90
    ;G1 X{x} Y{y} F6000
    G1 X250 Y20 F6000






# --------------------------
# T1电机的独立配置   260408 雙擠出機配置 # Driver4
# --------------------------
[extruder_stepper extruder_t1]
# 初始不绑定，开机不激活

extruder:
# T1电机的独立参数（完全自定义）
step_pin: PF9
dir_pin: !PF10
enable_pin: !PG2
microsteps: 32
full_steps_per_rotation: 200
rotation_distance: 4.69
;gear_ratio: 50:17

# T1电机驱动配置
[tmc2209 extruder_stepper extruder_t1]
uart_pin: PF2
run_current: 0.6
interpolate: false

# --------------------------
# 换刀切换宏
# --------------------------
# 激活T0电机
[gcode_macro T0]
gcode:
    # 解绑T1电机
    SYNC_STEPPER_TO_EXTRUDER STEPPER=extruder_t1 EXTRUDER=
    # 激活T0电机绑定到主挤出机
    SYNC_STEPPER_TO_EXTRUDER STEPPER=extruder EXTRUDER=extruder
    M117 Activated T0

# 激活T1电机
[gcode_macro T1]
gcode:
    # 解绑T0电机
    SYNC_STEPPER_TO_EXTRUDER STEPPER=extruder EXTRUDER=
    # 激活T1电机绑定到主挤出机
    SYNC_STEPPER_TO_EXTRUDER STEPPER=extruder_t1 EXTRUDER=extruder
    M117 Activated T1


















# This file contains common pin mappings for the BigTreeTech Octopus
# and Octopus Pro boards. To use this config, start by identifying the
# micro-controller on the board - it may be an STM32F446, STM32F429,
# or an STM32H723.  Select the appropriate micro-controller in "make
# menuconfig" and select "Enable low-level configuration options". For
# STM32F446 boards the firmware should be compiled with a "32KiB
# bootloader" and a "12MHz crystal" clock reference. For STM32F429
# boards use a "32KiB bootloader" and an "8MHz crystal". For STM32H723
# boards use a "128KiB bootloader" and a "25Mhz crystal".

# See docs/Config_Reference.md for a description of parameters.


#####################################################################
#             X/Y步进电机设置 (X/Y Stepper Settings)                 # 
#####################################################################
#   B Motor ---- Motor A 
#   |                  |
#   |------挤出机-------|
#   |                  |
#   |                  |
#          正前方   






#####################################################################
#                          X 轴步进电机   (B 电机)                    #
#####################################################################


# Driver0
[stepper_x]
step_pin: PF13                       # X轴电机脉冲引脚设置
dir_pin: PF12                        # X轴电机运行引脚设置,方向按实际判断，加感叹号会让运行方向反转
enable_pin: !PF14                    # X轴电机使能引脚设置,使能引脚需要加感叹号，否者电机不工作
rotation_distance: 40               # 主动带轮周长mm（2GT-20T带轮40，2GT-16T带轮32）
microsteps: 8                      # 电机细分设置，细分越高，质量越高，但主控负荷越大
full_steps_per_rotation: 200        # 电机单圈所需脉冲数（1.8度电机:200，0.9度电机:400）
endstop_pin: PG6                   # 限位开关PIN脚,建议常闭然后添加！反转状态,位置在io-3
###接常闭后是触发状态，加感叹号可以反转这个状态，万一断线时候可以避免撞机
position_min: 0                     # 软限位最小行程
position_endstop: 300               # 软限位最大行程 (250mm-300mm-350mm)
position_max: 300                   # 机械限位最大行程 (250mm-300mm-350mm)
homing_speed: 80                    # 复位速度，最大为100.归位速度建议别太快
homing_retract_dist: 5              # 第一次触发复位开关之后的后退距离
homing_positive_dir: true           # 复位方向（一般不需要改动）
# step_pulse_duration: 0.000004



#####################################################################
#                       y 轴步进电机   (A 电机)                       #
###################################y##################################
#Y电机口
# Driver1
[stepper_y]
step_pin: PG0                       # Y轴电机脉冲引脚设置
dir_pin: PG1                      # Y轴电机运行引脚设置,方向按实际判断，加感叹号会让运行方向反转
enable_pin: !PF15                   # Y轴电机使能引脚设置,使能引脚需要加感叹号，否者电机不工作
rotation_distance: 40               # 主动带轮周长mm（2GT-20T带轮40，2GT-16T带轮32）
microsteps: 8                      # 电机细分设置，细分越高，质量越高，但主控负荷越大
full_steps_per_rotation: 200        # 电机单圈所需脉冲数（1.8度电机:200，0.9度电机:400）
endstop_pin: PG9                   # 限位开关PIN脚,建议常闭然后添加！反转状态,位置在io-0
###接常闭后是触发状态，加感叹号可以反转这个状态，万一断线时候可以避免撞机
position_min: 0                     # 软限位最小行程
position_endstop: 300               # 软限位最大行程 (250mm-300mm-350mm)
position_max: 300                   # 机械限位最大行程 (250mm-300mm-350mm)
homing_speed: 80                    # 复位速度，最大为100        归位速度建议别太快
homing_retract_dist: 5              # 第一次触发复位开关之后的后退距离
homing_positive_dir: true           # 复位方向（一般不需要改动）
# step_pulse_duration: 0.000004


#####################################################################
#                     Z轴步进电机 （Z Stepper Settings）              #
#####################################################################
#  Z1-------------Z2
#   |              |
#   |              |
#   |              |
#  Z0----显示屏----Z3

#####################################################################
#                           Z轴步进电机                              #
#####################################################################



# Driver2
##  Z步进电机 - 左前方 z接口
[stepper_z]
step_pin: PF11                 # z轴电机脉冲引脚设置
dir_pin: PG3                 # z轴电机方向引脚设置,方向引脚需要按实际判断，加感叹号会让运行方向反转
enable_pin: !PG5              # z轴电机方向引脚设置,方向引脚需要按实际判断，加感叹号会让运行方向反转
rotation_distance: 40         # 主动轮周长mm （2GT-20T为 40mm  16T为 32mm）
gear_ratio: 80:16             # 减速比
full_steps_per_rotation: 200  # 电机单圈所需脉冲数（1.8度电机:200，0.9度电机:400
microsteps: 8                # 电机细分设置,细分越高，质量越高，但主控负荷越大
endstop_pin: !PG10             # 限位开关PIN脚,建议常闭然后添加！反转状态,位置在io-1
# endstop_pin: probe:z_virtual_endstop # for tap
position_endstop: -5
## position_endstop 是喷嘴相对于打印表面(Z0)到Z限位停止触发点的位置(单位:mm)
## 正数值 = 高于平台的终止点，负数值 = 低于平台的的终止点
## 增加position_endstop的数值会使喷嘴更靠近床
## 在运行Z_ENDSTOP_CALIBRATE之后，position_endstop将存储在CFG配置的最后
position_min: -10             # （配置喷嘴清洁需要-5左右）
position_max: 300             # 机械限位最大行程 (250mm-300mm-350mm)
homing_speed: 10               # 复位速度-最大 20
second_homing_speed: 3        # 二次复位速度-最大 10
homing_retract_dist: 5        # 后撤距离
# step_pulse_duration: 0.000004
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

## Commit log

2026-01-11 fixed typos and used "cementitious" as a better fit
    cement-based materials (cement paste, mortar, concrete) , or even more kinds of non-Newtonian fluid, are expected to work in this concept of vibration printing.
2026-04-01 slice setting fyr.
    Different mixtures may need different parameters.
    [260328 vcp voron nz3, voron cube n benchy.3mf]
2026-04-23 major cad upload
    all visible parts are good, but not the feed screw.
    i tried the M5 shaft feed screw but failed, so we may go back to M3 shaft feed screw (upload seperately.
2026-04-23 klipper printer.cfg reference
    [260423 vcp voron klipper configuration reference, printer.cfg]
2026-04-23 slice reference, voron cube
    [260423 vcp voron nz3, slice reference.3mf]
2026-04-25 toolhead intro updated
2026-04-25 assembly updated
2026-06-22 vcp voron r11 major CAD file
2026-06-22 r11 toolhead intro section added
2026-06-22 260622 update, 100% sizer 3dbenchy printed!
